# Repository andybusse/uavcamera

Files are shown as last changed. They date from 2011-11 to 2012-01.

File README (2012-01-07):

Unmanned Aircraft Camera Module

(Full specification including deliverables for this project is contained in documents/specification/Agreed_Spec_Gantt_GDP18.pdf)

Repository Structure:
- ArduinoCore: An Eclipse project that creates an Arduino library, allowing us to combine Arduino code with AVR C Source code.
- documents: Project Management foo, foo that requires submission (reports, presentations + whatnot), minutes of meetings, etc.
- eclipse:
    - CamPayloadCpp: source code for the payload controller firmware (not all ours)
        - mod: existing code from our customer
	- sanguino: code from the sanguino project (http://sanguino.cc)
	- SoftwareSerial - the SoftwareSerial library for Arduino/Sanguino (http://www.arduino.cc/en/Reference/SoftwareSerial)
	- SD: the SD library for Arduino/Sanguino (http://www.arduino.cc/en/Reference)
    - progressiveJPEG2: our current work on progressive jpeg encoding/decoding
- ExtractorExecutable: final version of custom JPEG extractor code (from progressiveJPEG2)
- FinalReport: our final report. RC2 is the version as handed in. Includes a CD with this repository at revision b0a90776af
- gettingJPEGdataInC: reads data from the camera and inserts this into a table.
- jpegCheaderExtractor(_nonavr): our current work on progressive jpeg encoding/decoding
- jpeghuffman: generates a huffman tree from a given JPEG image.
- Matlab: Matlab code to test custom image compression methods.
- NCamGS: Code for our ground station image viewer (C#, Visual Studio 2010 project)
- programAVR: Slightly modified from sample_peripheral, code intended to be run on a DIP version of the ATmega168.
- progressiveJPEG2: our current work on progressive encoding/decoding
- sample_peripheral: Schematics and Code for a simple AVR-based peripheral for the autopilot module. Supplied by the customer.
- schematics: A full set of schematics, PCB layout and gerber files generated using gschem and PCB from the gEDA toolsuite. Run "$ gschem $NAME.sch 
- uCode: Arduino "sketch" code, written for an Arduino Uno, designed to communicate with our chosen camera, implementing the commands defined in the datasheet (linked to within documents/)
    - SPI_debugger: code for the SPI debugger, based on an example project in the Arduino IDE (http://www.arduino.cc)

This project also contains some code which we have not authored:
    - ArduinoCore (from http://www.arduino.cc)
    - eclipse/ArduinoCore (from http://www.arduino.cc)
    - eclipse/ArduinoBlinkTest_Template (from http://www.arduino.cc)
    - eclipse/CamPayloadArduino/SD (from http://www.arduino.cc/en/Reference)
    - eclipse/CamPayloadArduino/SoftwareSerial (from http://www.arduino.cc/en/Reference/SoftwareSerial)
    - sample_peripheral - existing code, provided by our customer (see below)
    - programAVR - essentially contains the same as sample_peripheral, just in a AVR Studio 5 project.

A Group Design Project (ELEC6050) - School of Electronics and Computer Science, University of Southampton.

GDP Group 18 Members:
Andrew Busse <Andrew.Busse@zepler.net>
John Charlesworth <jgac1g08@ecs.soton.ac.uk>
Michael Hodgson <mh23g08@ecs.soton.ac.uk>
Paramithi Svastisinha <ps6g08@ecs.soton.ac.uk>
Piyabhum Sornpaisarn <ps26g08@ecs.soton.ac.uk>

Supervisor: Dr. Rob Maunder <rm@ecs.soton.ac.uk>
Customer: Dr. Matt Bennett <m.bennett@skycircuits.com>

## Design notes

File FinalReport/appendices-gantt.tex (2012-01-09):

% This is part of the FinalReport document.
% Copyright (C) 2011 Piyabhum Sornpaisarn, Andrew Busse, Michael Hodgson, John Charlesworth, Paramithi Svastisinha
% See the file COPYING in FinalReport/ for copying conditions.

\label{appendix:gantt}
This section shows the Gantt Charts produced for this project. The first one, 
displayed over the first three pages, shows our initial Gantt chart, as 
produced for handin with the specification (10th October 2011).

The second, shown over pages 4 to 6, shows a revised version of our Gantt 
Chart, produced on 8th November 2011.

The third, shown over pages 7 to 9 shows the final version of our Gantt chart as of
15th December 2011.

These Gantt Charts have been produced using the Planner tool from GNOME office.
\footnote{\url{http://live.gnome.org/Planner}}

\includepdf[scale=1.0,pages={1-3},offset=25mm -25mm]{gantt/gantt1.pdf}
\includepdf[scale=1.0,pages={1-3},offset=25mm -25mm]{gantt/gantt2.pdf}
\includepdf[scale=1.0,pages={1-3},offset=25mm -25mm]{gantt/ganttfinal.pdf}

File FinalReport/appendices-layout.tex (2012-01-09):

% This is part of the FinalReport document.
% Copyright (C) 2011 Piyabhum Sornpaisarn, Andrew Busse, Michael Hodgson, John Charlesworth, Paramithi Svastisinha
% See the file COPYING in FinalReport/ for copying conditions.

\label{appendix-layout}

The layout of the final PCB module. As seen in figure \ref{fig:PayloadImplementation} 

This was made using PCB \footnote{\url{http://geda.seul.org/wiki/geda:gaf}} from the gEDA toolsuite.

Gerber files, and full source files, are available in our central GitHub 
\cite{github} repository, under schematics/payload\_644.pcb and schematics/gerbers

Running
\begin{verbatim} 
$ gsch2pcb projectrc
\end{verbatim}
from within schematics/ should update any changes you make to payload\_644.sch.

\begin{figure}[H]
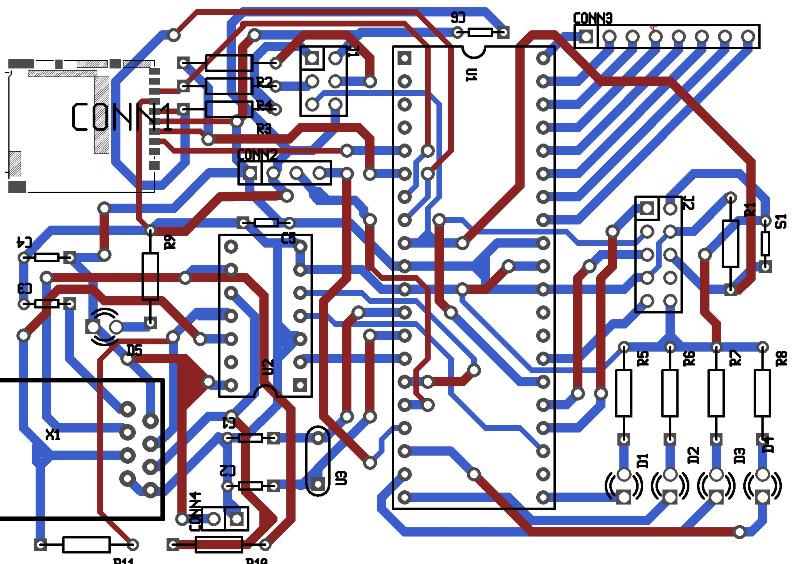
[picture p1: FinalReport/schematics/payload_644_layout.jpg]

\caption{Layout of our delivered PCB module. Dark Red: component layer. Light Blue: solder layer}
\end{figure}

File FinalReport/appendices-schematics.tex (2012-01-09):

% This is part of the FinalReport document.
% Copyright (C) 2011 Piyabhum Sornpaisarn, Andrew Busse, Michael Hodgson, John Charlesworth, Paramithi Svastisinha
% See the file COPYING in FinalReport/ for copying conditions.

\label{appendix_schematics}

All schematics in this Appendix were generated using gschem from the gEDA 
toolsuite. \footnote{\url{http://geda.seul.org/wiki/geda:gaf}}

These are all available in our GitHub repository \cite{github}, under the 
schematics/ folder. PDF and PS files are also available in the 
schematics/images folder.

Note that you need to run 
\begin{verbatim} 
$ gschem SCHEMATIC_NAME
\end{verbatim}
from within this folder to use the non-standard symbols available in that 
folder.

\section{Dummy Payload}
\begin{figure}[H]

\caption{Schematic of the circuit used to test communication from a "dummy" 
payload to the autopilot module. Largely based on a schematic provided by 
our customer, and runs a slightly modified version of source code provided 
again, by our customer.}
\end{figure}

\section{Final Payload Module}
\label{Payload_Schematic}
\begin{figure}[H]

\caption{Final Schematic of the implemented payload module. See \ref{fig:PayloadImplementation} for a 
detailed explanation of which components are for what purpose}
\end{figure}

\section{Payload: Arduino Uno with additional ATmega168}
\begin{figure}[H]

\caption{Schematic for a considered payload module: an 
Arduino Uno with a daughter board containing an ATmega168 for Autopilot to 
Payload module communication.}
\end{figure}

\section{Payload: Arduino Uno with Multiplexed UART line}
\begin{figure}[H]

\caption{Schematic for a considered payload module: an 
Arduino Uno with its UART line multiplexed between camera and autopilot 
communication}
\end{figure}

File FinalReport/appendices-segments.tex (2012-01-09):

% This is part of the FinalReport document.
% Copyright (C) 2011 Piyabhum Sornpaisarn, Andrew Busse, Michael Hodgson, John Charlesworth, Paramithi Svastisinha
% See the file COPYING in FinalReport/ for copying conditions.

\section{SOF0: Start Of Frame (0xc0):}

\begin{table}[!hbtp]
	\label{sof-content}
	\caption{SOF0 Marker Content}
	\centering
	\begin{tabular}{ | p{2cm} | p{1.5cm} | p{4cm} | }
	\hline
	\textbf{Field} & \textbf{Size} & \textbf{Comments} \\ \hline
	Length & 2 bytes & Equal to 8 + the number of components used in the colour scheme * 3\\ \hline
	Data precision & 1 byte & Value shown in bits/sample. Usually 8 signifying bytes.\\ \hline
	Image height  & 2 bytes & ----\\ \hline
	Image width  & 2 bytes & ----\\ \hline
	Number of components & 1 byte & indicates the number of components used  in the colour scheme\\ \hline
	Component information & 3 bytes / component & See component information table below.\\ \hline
	\end{tabular}
\end{table}

\begin{table}[!hbtp]
	\label{sof-comp-content}
	\caption{SOF Component Information}
	\centering
	\begin{tabular}{ | p{2cm} | p{4cm} | }
	\hline
	\textbf{Byte Number} &  \textbf{Information} \\ \hline
	1 & Component ID (1 = Y, 2 = Cb, 3 = Cr, 4 = I, 5 = Q)\\ \hline
	2 & Sampling factors (bits 0\ldots3 : vertical, bits 4\ldots7 horizontal)\\ \hline
	3 & Quantization table number\\ \hline
	\end{tabular}
\end{table}

\newpage

\section{DHT: Define Huffman Table(s) (0xc4):}

\begin{table}[!hbtp]
	\label{dht-content}
	\caption{DHT Marker Content}
	\centering
	\begin{tabular}{ | p{2cm} | p{1.5cm} | p{4cm} | }
	\hline
	\textbf{Field} & \textbf{Size} & \textbf{Comments} \\ \hline
	Length & 2 bytes & ----\\ \hline
	HT Information & 1 byte & See HT Information table below\\ \hline
	Number of Symbols  & 16 bytes & Number of symbols with codes of length 1\ldots16.
	The sum of these values (\emph{n})must be $\le$ 256\\ \hline
	Symbols  & \emph{n} bytes & Symbols of the HT in order of increasing code length\\ \hline
	\end{tabular}
\end{table}

\begin{table}[!hbtp]
	\label{dht-info-content}
	\caption{HT Information Byte Content}
	\centering
	\begin{tabular}{ | p{2cm} | p{4cm} | }
	\hline
	\textbf{Bit} &  \textbf{Information} \\ \hline
	0\ldots3 & ID number of HT\\ \hline
	4 & type of HT, 0 = DC table, 1 = AC table\\ \hline
	5\ldots7 & Unused\\ \hline
	\end{tabular}
\end{table}

\section{DQT: Define Quantization Table(s) (0xdb):}

\begin{table}[!hbtp]
	\label{dqt-content}
	\caption{DQT Marker Content}
	\centering
	\begin{tabular}{ | p{2cm} | p{1.5cm} | p{4cm} | }
	\hline
	\textbf{Field} & \textbf{Size} & \textbf{Comments} \\ \hline
	Length & 2 bytes & ----\\ \hline
	QT Information & 1 byte & See QT Information table below\\ \hline
	Bytes  & \emph{n} bytes & QT values. \emph{n} = 64 * (QT precision + 1) \\ \hline
	\end{tabular}
\end{table}

\begin{table}[!hbtp]
	\label{dqt-info-content}
	\caption{QT Information Byte Content}
	\centering
	\begin{tabular}{ | p{2cm} | p{4cm} | }
	\hline
	\textbf{Bit} &  \textbf{Information} \\ \hline
	0\ldots3 & ID number of QT\\ \hline
	4\ldots7 & precision of QT (0 = 8 bit, else 16 bit)\\ \hline
	\end{tabular}
\end{table}

\newpage

\section{SOS: Start Of Scan (0xda):}

\begin{table}[!hbtp]
	\label{sos-content}
	\caption{SOS Marker Content}
	\centering
	\begin{tabular}{ | p{2cm} | p{1.5cm} | p{4cm} | }
	\hline
	\textbf{Field} & \textbf{Size} & \textbf{Comments} \\ \hline
	Length & 2 bytes & Equal to 6 + 2 * (number of components in scan)\\ \hline
	Number of components in scan & 1 byte & Within range 1 to 4\\ \hline
	Component information & 2 bytes / component & See component information table below.\\ \hline
	Ignorable Bytes & 3 bytes & Separates header information from entropy-encoded image data\\ \hline
	\end{tabular}
\end{table}

\begin{table}[!hbtp]
	\label{sof-comp-content}
	\caption{SOS Component Information Content}
	\centering
	\begin{tabular}{ | p{2cm} | p{4cm} | }
	\hline
	\textbf{Byte Number} &  \textbf{Information} \\ \hline
	1 & Component ID (1 = Y, 2 = Cb, 3 = Cr, 4 = I, 5 = Q)\\ \hline
	2 & HT to use (bits 0\ldots3 : AC Table ID, bits 4\ldots7 DC Table ID)\\ \hline
	\end{tabular}
\end{table}

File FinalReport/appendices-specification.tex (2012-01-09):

% This is part of the FinalReport document.
% Copyright (C) 2011 Piyabhum Sornpaisarn, Andrew Busse, Michael Hodgson, John Charlesworth, Paramithi Svastisinha
% See the file COPYING in FinalReport/ for copying conditions.

\label{initial_spec}

This Specification is our specification as it was submitted on to C-BASS 
on Monday 10th October 2011

\includepdf[scale=1.0,pages={1,2},offset=14mm -20mm]{spec/Agreed_Spec_GDP18.pdf}

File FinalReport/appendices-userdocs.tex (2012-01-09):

% This is part of the FinalReport document.
% Copyright (C) 2011 Piyabhum Sornpaisarn, Andrew Busse, Michael Hodgson, John Charlesworth, Paramithi Svastisinha
% See the file COPYING in FinalReport/ for copying conditions.

\label{userDocs}

\includepdf[scale=1.0,pages={1,2,3,4,5,6,7},offset=14mm -20mm]{docs/userGuide.pdf}

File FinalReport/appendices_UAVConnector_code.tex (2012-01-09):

% This is part of the FinalReport document.
% Copyright (C) 2011 Piyabhum Sornpaisarn, Andrew Busse, Michael Hodgson, John Charlesworth, Paramithi Svastisinha
% See the file COPYING in FinalReport/ for copying conditions.

\lstset{numbers=left,
numberstyle=\footnotesize, 
stepnumber=2,numbersep=5pt}
\section{\texttt{UAVConnector} Class}
\begin{lstlisting}[caption=\texttt{UAVConnector} Class, label=appen:UAVConnector]
using System;
using System.Collections.Generic;
using System.Linq;
using System.Text;
using System.Net.Sockets;
using System.Net.Configuration;
using System.IO;

namespace NCamGS
{
    class UAVConnector
    {
        Socket dataPort = new Socket(AddressFamily.InterNetwork, SocketType.Stream, ProtocolType.Tcp);
        Socket consolePort = new Socket(AddressFamily.InterNetwork, SocketType.Stream, ProtocolType.Tcp);

        public void Connect(byte dataStream)
        {
            try
            {
                dataPort.Connect("localhost", 8802);
                //MessageBox.Show("Connection to Port Name" + portName + "Port Number" + portNumber + "is complete!");
                Console.WriteLine("Data port connection to Port Name {0}  Port Number {1} is complete!", "localhost", 8802);

                // send selection byte to select datastream 0
                byte[] dataStreamSelection = { dataStream };
                dataPort.Send(dataStreamSelection);
                Console.WriteLine("Data stream selection completed.");

                consolePort.Connect("localhost", 8800);
                Console.WriteLine("Data port connection to Port Name {0} Port Number {1} is complete!", "localhost", 8800);
            }
            catch
            {
                Console.WriteLine("Error code\n Unable to connect to UAV:\n Please check that:\n1.The UAV is connected \n2.The program gcs has opened \n3. The program has connect to the UAV\n4.The program has send stream dat\n5. The program as to run testbyte on da");
                //MessageBox.Show("Error code\n Unable to connect to UAV:\n Please check that:\n1.The UAV is connected \n2.The program gcs has opened \n3. The program has connect to the UAV\n4.The program has send stream dat\n5. The program as to run testbyte on da");
            }
        }

        public byte[] GetDataBytes()
        {
            //byte[] getByteSendBytes = new byte[numBytes]; // you need to send 0's to get bytes out for some reason (NOPE, it does not)
            //for(int i = 0; i < numBytes; i++) {
            //    getByteSendBytes[i] = 0;
            //}
            //dataPort.Send(getByteSendBytes);
            byte[] sizeByte = { 0 };
            try
            {
                dataPort.Receive(sizeByte, 1, SocketFlags.None);
            }
            catch
            {
                
            }
            int numBytes = sizeByte[0];
            byte[] recBytes = new byte[numBytes];
            try
            {
                dataPort.Receive(recBytes, numBytes, SocketFlags.None);
            }
            catch
            { 
                
            }
            return recBytes;
        }

        public void SendTextToUAV(string textToUAV)
        {
            char[] toUAVChar = new char[512];
            byte[] toUAVByte = new byte[512];
            byte[] fromUAVByte = new byte[1000];
            byte[] oneByteArray = new byte[1];
            textToUAV += "\n";
            toUAVChar = textToUAV.ToCharArray();
            toUAVByte = System.Text.Encoding.ASCII.GetBytes(toUAVChar);
            try
            {
                int sendByte = consolePort.Send(toUAVByte, toUAVChar.Length, SocketFlags.None);
            }
            catch (SocketException ex)
            {
                Console.WriteLine("ERROR: " + ex.Message);
            }
        }
        public void SendCommand(byte[] command)
        {
            // use to send commmand to the uav
            string toUAV;
            //string fromUAV;
            char[] toUAVChar = new char[512];
            byte[] toUAVByte = new byte[512];
            byte[] fromUAVByte = new byte[1000];
            byte[] oneByteArray = new byte[1];

            toUAV = "payload[0].send_bytes";

            for (int commandByteCount = 0; commandByteCount < command.Length; commandByteCount++)
            {
                oneByteArray[0] = command[commandByteCount];
                toUAV += " 0x" + BitConverter.ToString(oneByteArray);
                //toUAV += " 0x" +System.Text.Encoding.ASCII.GetString(oneByteArray); 
            }

            toUAV += "\n";
            toUAVChar = toUAV.ToCharArray();
            toUAVByte = System.Text.Encoding.ASCII.GetBytes(toUAVChar);
            try
            {
                int sendByte = consolePort.Send(toUAVByte, toUAVChar.Length, SocketFlags.None);
            }
            catch (SocketException ex)
            {
                Console.WriteLine("ERROR: " + ex.Message);
            }
            //Port.Receive(fromUAVByte);
            //fromUAV = System.Text.Encoding.ASCII.GetString(fromUAVByte);
        }

        public void Close()
        {
            dataPort.Close();
        }

    }
}
\end{lstlisting}

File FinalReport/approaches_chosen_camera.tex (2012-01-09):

% This is part of the FinalReport document.
% Copyright (C) 2011 Piyabhum Sornpaisarn, Andrew Busse, Michael Hodgson, John Charlesworth, Paramithi Svastisinha
% See the file COPYING in FinalReport/ for copying conditions.

\section{Camera module}
\label{sec:John_chosen_options}

The camera type chosen was a serial camera as described in \ref{sec:Serial_option}. The particular model chosen was uCam (microCam) or the "Camera Module - Serial JPEG TTL" from the "coolcomponents" website.

The feature set of the uCam is as follows:
	\begin{itemize}
		\item It can output images in both RAW and jpeg formats
		\item It can output RAW images at a range of resolutions:
		\begin{itemize}
			\item 80 x 60
			\item 160 x 120
			\item 320 x 240
			\item 640 x 480
			\item 128 x 128
			\item 128 x 96
		\end{itemize}
		\item It can output jpeg images at a range of resolutions:
		\begin{itemize}
			\item 80 x 64
			\item 160 x 128
			\item 320 x 240
			\item 640 x 480
		\end{itemize}
		\item it can output RAW images with a range of colour settings:
		\begin{itemize}
			\item 2bit Gray Scale
			\item 4bit Gray Scale
			\item 8bit Gray Scale
			\item 8bit Colour
			\item 12bit Colour
			\item 16bit Colour
		\end{itemize}
		\item It will auto-detect baud rates from 14400 to 115200
		\item It has selectable baud rates up to 1228800
		\item Small physical size at 32mm x 32mm
		\item Well documented
	\end{itemize}

The camera was chosen because this feature set meets the specification and also allows for additional functionality, such as setting the resolution, if the full feature set is exploited.

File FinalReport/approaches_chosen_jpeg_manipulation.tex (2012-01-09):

% This is part of the FinalReport document.
% Copyright (C) 2011 Piyabhum Sornpaisarn, Andrew Busse, Michael Hodgson, John Charlesworth, Paramithi Svastisinha
% See the file COPYING in FinalReport/ for copying conditions.

\section{Progressive JPEG Manipulation}

\subsection{JPEG Manipulation}

Prior to knowing the exact speed it would take to send an image from the camera to the ground station, 
it was decided that custom JPEG manipulation would optimize the image further and help reach the target time specified. 
Therefore, tasks concerning the custom manipulation of the JPEG image were planned and worked on at the beginning of the project. 
However, when a working module was constructed, the time needed to send the image was already well within the specified time. 
Because this was the primary advantage of the custom JPEG manipulation process, the task's priority was dropped accordingly.

\subsection{JPEG Data Access}

The dynamic form of data accessing was preferred due to the memory contraints imposed on the device.

\subsection{Entropy-Encoded Data Storage}

The entropy-encoded data will be stored as chrominance pixels for the sake of clarity. 
It is also a method which could be coded more easiliy than seperate component storage. 
This allowed the extractor to work with the progressive JPEG encoder sooner to avoid the task from overrunning.

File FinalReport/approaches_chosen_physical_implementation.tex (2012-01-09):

% This is part of the FinalReport document.
% Copyright (C) 2011 Piyabhum Sornpaisarn, Andrew Busse, Michael Hodgson, John Charlesworth, Paramithi Svastisinha
% See the file COPYING in FinalReport/ for copying conditions.

\section{Physical Implementation}

The physical implementation of the payload has taken many forms, reflecting 
the each of the design-prototype-test cycles that our group experienced.

\begin{itemize}
\item Initially, the system was built in two separate parts: The first was 
the modified version of the ATmega168P-based sample schematic provided by 
our customer, which handled communication to the payload port of the 
autopilot. The second was an Arduino Uno R2 with its Serial (UART) line 
connected to the camera and an SPI connection to an SD card. This system 
simply took an image from the camera and wrote it to the SD card. The SD card 
to Arduino connection was via some protoboard and an SD card reader breakout 
board on loan from Zepler Stores.
\item The next design iteration used an "Il Matto" board and daughter board, 
designed for 2011's D4 lab (a two-week Design and Build exercise for second 
year Electronic Engineers). The board itself is rather simple - an ATmega644P 
with all of its ports connected to expansion headers, an SPI line connection 
to an SD card reader, and power taken from a mini-USB connection, stepped 
down to 3V3 by a linear regulator. A daughter board (which slots into the 
expansion headers) has the transceiver to communicate with the autopilot

This implementation of the payload contains all the elements of the final 
schematic, so technically could be test-flown.
\item Whereas the above approach would technically fulfil the specification, 
implementing it would be expensive: the Il Matto boards were one-off boards 
designed specifically for a lab, so a customer would certainly need to 
manufacture and build their own, including the daughter board. Having this as 
a single PCB solution would be a lot neater, smaller, lighter and cheaper.

Therefore, a final PCB was designed (this is elaborated upon in 
\ref{sec:PCB-implementation}), specific to our application, with all the 
features we need. Only through-hole components are used where possible, 
making the task of soldering components to the PCB as easy as possible.
\end{itemize}

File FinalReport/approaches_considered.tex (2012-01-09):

% This is part of the FinalReport document.
% Copyright (C) 2011 Piyabhum Sornpaisarn, Andrew Busse, Michael Hodgson, John Charlesworth, Paramithi Svastisinha
% See the file COPYING in FinalReport/ for copying conditions.

%% ----------------------------------------------------------------
\chapter{Design Decisions}
%% ----------------------------------------------------------------
Throughout the design and implementation of the project there were many points
at which decisions were made about the design of the system. This chapter attempts
to give an insight into some of the design decisions taken throughout the project with
a discussion of the alternative choices that were open to us at the time and the reasons
why a particular choice was made.

This chapter also details thel milestones of the project. These milestones can be seen in section \ref{sec:amended_milestones}.

\input{approaches_considered_camera}

\input{approaches_considered_local_storage}

\input{approaches_considered_payload}

\input{approaches_considered_jpeg_manipulation}

\input{approaches_considered_GUI}

\section{Physical Implementation (ab)}

Our specification states that the final module delivered to the customer 
should be on PCB, if time permits. Using existing breakout board type devices 
(such as the Arduino) and a daughter board would make the project far cheaper for 
one-off applications (one-off PCBs can be rather expensive) while still fitting 
this specification point, 
but would increase construction time to reproduce it, and increase the weight 
and volume of the module, two critical components of the project.

However, producing a bespoke PCB has the advantage of being smaller 
and lighter, and assembly could be handled by an external company.

Producing a stripboard solution would be implemented only if time and budgetary constraints are against us: 
whilst being the cheapest option, it would be larger than a PCB solution and not as robust.
	
\subsection{Power Source}

We also need to consider how such a module will be powered, and plan for both the following considerations:

\subsubsection{Approach: Battery Powered}

Providing a header on our final payload to attach an external power source 
should the Autopilot not be able to provide enough power would seem a 
sensible option. As this battery is likely to be Lithium-Ion or 
Lithium-Polymer, implementing a charging circuit may be considered, but would 
be dangerous to test. (Lithium Polymer batteries are prone to damage if incorrectly charged)

\subsubsection{Approach: Autopilot Powered}

It should be possible to source enough power from the Autopilot, which can 
comfortably provide up to 200mA at 3.3V. Designing our module to be as low-powered 
as possible would be beneficial (this extends the time the autopilot will be 
able to fly)

\input{milestones_amended}

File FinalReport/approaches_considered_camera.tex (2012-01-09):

% This is part of the FinalReport document.
% Copyright (C) 2011 Piyabhum Sornpaisarn, Andrew Busse, Michael Hodgson, John Charlesworth, Paramithi Svastisinha
% See the file COPYING in FinalReport/ for copying conditions.

\section{Camera Module (jc)}
\label{sec:John_options}

A range of different camera modules were researched and considered for use in the project.

\subsection{Approach: Compact Digital Camera}
\label{sec:Compact_option}
A huge range of compact digital cameras are available for purchase and this was considered as a possible approach.

Advantages:
      \begin{itemize}
         \item High resolution of typically 5+ Megapixels.
		 \item Fully encapsulated.
		 \item High quality images possible thanks to automatic focus and zoom.
     \end{itemize}

Disadvantages:
     \begin{itemize}
        \item Difficult/impossible to communicate with: most modern digital cameras have a USB socket for downloading images off the camera but it is much rarer to be able to send the camera commands (e.g. take photo) and for those cameras where it is possible the command structure is not usually simple.
        \item Requires USB host device in order to properly communicate as only USB host devices provide power via USB and can have USB peripherals connected to them.
	\item Relatively large and heavy compared to the other approaches considered.
	\item Expensive, prices starting around \pounds 60.
     \end{itemize}

In order to communicate with a camera via USB a USB host is required. The process is usually fairly complex so driver is normally used. This is extremely difficult to implement on a device compact enough for use in this project.

\subsection{Approach: USB Camera}
\label{sec:USB_option}
Many USB webcams are available for purchase and this was considered as a possible approach.

Advantages:
      \begin{itemize}
         \item Low cost of typically around \pounds 15.
         \item High resolution of typically 1 to 3 Megapixels.
		 \item Small size of usually less than 50mm by 50mm.
		 \item Cabling included so can be easily positioned in the UAV.
     \end{itemize}

Disadvantages:
\begin{itemize}
     \item Often poorly documented: no datasheets or datasheets aimed solely at use with a computer.
     \item Difficult to communicate with: These devices are usually designed to be used with a computer so communication is usually done using a proprietary driver (a piece of software that defines how to interact with a peripheral). In order to maintain the proprietary nature of these documentation and/or source code is often not available for them.
    \item Requires USB host device in order to properly communicate as only USB host devices provide power via USB and can have USB peripherals connected to them.
	\item High resolution means longer total transfer times, including time to transfer from the camera and time spent on any compression/ manipulation.
\end{itemize}

In order to communicate with a USB camera a USB host is required, and as the process is usually fairly complex a driver is normally used. These drivers are fairly complex pieces of code and they are designed for use on computers, they are also often poorly documented so it would be extremely difficult to implement them on a device compact enough for use in this project.

\subsection{Approach: Analogue Camera}
\label{sec:Analog_option}

Camera modules with analogue composite outputs are available, usually for cctv or surveilence purposes, and were also considered as an approach.

Advantages:
\begin{itemize}
	\item Range of resolutions available.
	\item Small size: usually less than 50mm x 50mm.
	\item This is a mature market so there are plenty of options available.
\end{itemize}

Disadvantages:
     \begin{itemize}
        \item Awkward to communicate with: in order to decode the output of these devices we either need to convert from analogue to digital and then decode the signal (this type of camera usually outputs in composite or component format both of which are complex encodings, particularly when converted to digital) or put the signal through a decoder IC which are better documented but still complex, and the correct chip must be used.
        \item Require case and cabling for placement in UAV.
		\item Can be expensive at up to around \pounds 80.
		\item Often video rather than still cameras.
		\item Often black and white rather than colour.
     \end{itemize}

There are a very wide range of cameras of this type available with different features however there is a significant amount of additional complexity introduced by the requirement to decode the analogue output into something that can be understood by a microcontroller.

\subsection{Approach: Serial Camera Module}
\label{sec:Serial_option}

Some camera modules are available with UART rather than USB serial communications and these to were considered as an approach.

Advantages:
      \begin{itemize}
      	 \item Well documented: these cameras usually come with datasheets and are often designed for use with electronic projects.
		 \item Easy to communicate with as they do not require a USB host or and analogue to digital conversion, additionally most microcontrollers have a built in UART port.
         \item Range of resolutions available.
		 \item Small size: usually less than 50mm x 50mm.
		 
     \end{itemize}

Disadvantages:
     \begin{itemize}
       	\item Require case and cabling for placement in UAV.
	\item Moderately expensive at around \pounds 40.
       	\item The lack of case means that the camera is susceptible to shorts and static.
     \end{itemize}

The ability to communicate via UART combined with the good documentation should allow for control to be established fastest with this camera type.

\section{Approach Chosen: Serial Camera module (jc)}
\label{sec:John_chosen_options}

The camera type chosen was a serial camera as described in \ref{sec:Serial_option}. We chose this camera type because it was the easiest to communicate with as it did not require a USB host or any kind of analogue to digital conversion and decoding. The serial camera type also has most of the advantages of the analogue camera type but is easier to communicate with.

The particular model chosen was uCam (microCam) or the "Camera Module - Serial JPEG TTL" from the "coolcomponents" website.

\begin{figure}[H]
        \centering
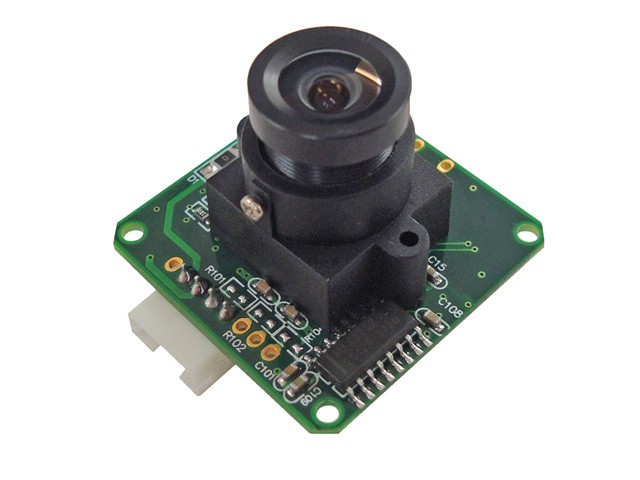
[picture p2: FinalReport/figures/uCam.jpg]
        
        \captionof{figure}{Photo of the 4D systems uCam, sourced from \cite{ucam_datasheet}}
        \label{fig:uCam_photo}
\end{figure}

The feature set of the uCam is as follows:

	\begin{itemize}
		\item It can output images in both RAW and jpeg formats
		\item It can output RAW images at a range of resolutions:
		\begin{itemize}
			\item 80 x 60
			\item 160 x 120
			\item 320 x 240
			\item 640 x 480
			\item 128 x 128
			\item 128 x 96
		\end{itemize}
		\item It can output JPEG images at a range of resolutions:
		\begin{itemize}
			\item 80 x 64
			\item 160 x 128
			\item 320 x 240
			\item 640 x 480
		\end{itemize}
		\item It can output RAW images with a range of colour settings:
		\begin{itemize}
			\item 2bit Gray Scale
			\item 4bit Gray Scale
			\item 8bit Gray Scale
			\item 8bit Colour
			\item 12bit Colour
			\item 16bit Colour
		\end{itemize}
		\item It will auto-detect baud rates from 14400 to 115200
		\item It has selectable baud rates up to 1228800
		\item Small physical size at 32mm x 32mm
		\item Well documented
	\end{itemize}

The camera was chosen because this feature set meets the specification and also allows for additional functionality, such as setting the resolution, if the full feature set is exploited.

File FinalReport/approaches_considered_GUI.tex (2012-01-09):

% This is part of the FinalReport document.
% Copyright (C) 2011 Piyabhum Sornpaisarn, Andrew Busse, Michael Hodgson, John Charlesworth, Paramithi Svastisinha
% See the file COPYING in FinalReport/ for copying conditions.

\section{Ground Station Image Viewer (ps)}

\subsection{Programming Language}

The decision depend on the team member who has been assigned as a task leader.
Because the program will be using to implement a GUI application, therefore it need an object oriented program for implementing this.
The programming languages that will be look into are Python, Javam and C\# programming language.
There are many factors to consider before the final decision is decide.

\subsubsection*{Python Language}
Python Language programming has variety of useful factors for network programming. 
The code on this language has been proved to be short and effective.
The class \texttt{ socket} has all the communication method which can be use. 
The TCP can be use by the program to send a text command on one machine to the another \cite{normanM}. 
There is a makefile function which the user can use to avoid the missing line of data or an extra line from next cycle of data\cite{normanM,guidoR}. 
It has support of GUI interface which the programmer can debug, and use a profiling tools \cite{sannerM}. 

Advantages:
\begin{itemize}
\item has a \texttt{socket()} class which can be use to connect to TCP/IP port
\item support GUI: it can use to create and debugging window application
\item can run with c code
\end{itemize}

Disadvantages:
\begin{itemize}
\item new to the developer
\item might be time consuming to learn if the developer has a same advantages in a familiar software
\end{itemize}

\subsubsection*{Java Language}
Java language is an object oriented program which can be use in any kind of operating system.
It derives some syntax from c/c++ which the developer is familiar to. 
This language has been using widely for applications and gaming and it also support the TCP class.
Java has two classes for TCP/IP, which are \texttt{Socket}, and \texttt{ServerSocket}.
At both ends of the communication can be identified by IP address and port number \cite{kennethC}.

Advantages:
\begin{itemize}
\item it object oriented program 
\item \texttt{Socket} and \texttt{ServerSocket }class support TCP/IP
\item support GUI application
\item has \texttt{graphic} class which can use to display images
\end{itemize}

Disadvantages:
\begin{itemize}
\item it can not inherit other language code to use in the program
\item the developer is not that familiar with the program
\item limit the effectiveness of customs protocols \cite{elliotH}
\end{itemize}

\subsubsection*{C\# Language}
C\# language is an object oriented program which can be use in any operating system.
It has ideally similar Socket class as the Java programming has. 
It also support the window application program.
The program has been use by the developer, therefore it can save time during the implementation of the program.

Advantages:
\begin{itemize}
\item familiar to the developer
\item \texttt{Socket} and \texttt{SerialPort} class support the TCP/IP connection
\item has graphic class which can use to display image
\item can make and debug window application 
\end{itemize}

The program that will be using to implement the program is C\# language. 
This is because the program is familiar with the user so it will save time of studying a new language.
It also support TCP/IP and window application which are main classes needed to implement the program.
Although Java and Python has been use by many papers and book on network programming, but it need to take time to learn a new language so the developer decided to use C\# \cite{normanM,guidoR,kennethC,elliotH}.

\subsection{Approach: Different C\# .NET Classes}
The C\# language on Microsoft Visual Basic Studio is a development environment for creating our Ground Station Image Viewer application. Choosing the right class to connect to the port helps the developer save time to program the application. 
 
\subsubsection{SerialPort Class}
The \texttt{System.IO.Ports} namespace contains classes for controlling serial ports. 
The \texttt{SerialPort} class is the most important one. It has ability to synchronous and event-driven I/O, access to pin and break states, and access to serial driver properties\cite{peak_netFrame}. 
By using this class, the COM port setting has to be memorized which will be simple to load and saves from/to disk.

\begin{lstlisting}[caption=Serial Port class connection\, read and write method, label=serialPortconn]
SerialPort( portName, baudRate, parity bit, dataBits, StopBits ) 
SerialPort.Read(Char(),Int32,Int32);
SerialPort.Write(Char(), Int32, Int32)	;
\end{lstlisting}

Advantage 
\begin{itemize}
\item can change baud rate, handshaking, parity bit, and stop bit
\item can change the internal of a hardware
\item can send and receive data from a defined connection
\item can program hardware
\end{itemize}
Disadvantage
\begin{itemize}
\item need to set up all the component (baud rate, handshaking, parity bit, and stop bit)
\item the set up make the code long and might cause error
\item the setting of the signal out must be the same as the set up in the UAV
\end{itemize}

\subsubsection{Socket Class}
The Socket is more programmer friendly, robust and a high level connection class. 
The program can easily connect to the port by using the method in Listing\ref{socketClasscrs} .
This class sends and array of bytes to the console port and to the data stream port and receive data from the port by code in Listing\ref{socketClasscrs}.

\begin{lstlisting}[caption=Socket class connect receive and send method,label=socketClasscrs]
Connect (String host name,Int32 port number)
Send(byte[] command, Int32 length, SocketFlags)
Receive(byte[] data, Int32 length, SocketFlags)
\end{lstlisting}

Advantage
\begin{itemize}
\item can set up the connection by simply stated the host name and port number
\item can connect to TCP/IP port 
\item it uses the set up of the port, therefore the parity, stop bit, and the baud rate are the same
\item can send and receive data from the port
\item can use delegates which give more flexibility on synchronous control of sockets \cite{robertH}
\end{itemize}
Disadvantage
\begin{itemize}
\item can not program hardware
\item can not set up the baud rate, stop bit or any other properties of the hardware
\end{itemize}

The socket class was the class chosen for the UAV port connector. 
It support TCP connection between the client and the server to do low level communication work\cite{xieX}. 
The changes of class improve efficiency of connection between port and the program. 
The baud rate and extra bits are automatically adjusted to be the same as the port, so the setting is identical between the input and output.

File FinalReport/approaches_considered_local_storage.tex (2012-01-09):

% This is part of the FinalReport document.
% Copyright (C) 2011 Piyabhum Sornpaisarn, Andrew Busse, Michael Hodgson, John Charlesworth, Paramithi Svastisinha
% See the file COPYING in FinalReport/ for copying conditions.

\section{Local Image Storage (ab)}
\label{sec:local_storage}

With a maximum image size of $640\times480$ pixels, an uncompressed JPEG 
image's file size would be approximately 900kB.
This is greater than the internal memory on the ATmega168, ATmega328 and 
ATmega644 (1KiB, 2KiB, and 4KiB respectively) microprocessors that were used 
during development of this project, therefore it cannot be guaranteed that a 
complete single image can be stored locally, without adding some extra memory.
\\
The advantages of being able to store a full image locally are:
\begin{itemize}
\item Would allow all original images taken during flight to be viewed once 
the UAV has been landed.
\item Would make the implementation of automatic repeat requests (resending of 
any corrupted payload -$>$ ground station packets) much easier.
\item Customer mentioned that currently, customers take images with their 
retrofitted cameras, but store the images locally instead of wirelessly 
transmitting them. Keeping the functionality to store all images taken 
on-board and then plug something into the ground station to view these once 
the UAV has been landed would be desirable, but not essential (hence why this 
is not mentioned in the specification).
\end{itemize}

The disadvantages:
\begin{itemize}
\item The material cost of the payload (in both component cost and PCB area) 
would be increased.
\item Addition of an extra component increases the project's complexity.
\end{itemize}

\subsection{Approach: Flash Chip}

One option considered was the implementation of an external flash memory chip 
(for evaluation purposes, the 4Mbit AMIC A25L040-F \cite{flash_datasheet} was purchased)

Advantages:
\begin{itemize}
\item Non-volatile memory. Allows data to be retained even if power to the payload module is cut off.
\item Excellent data integrity: ~100000 Write/Erase cycles, and $>$10 years data retention.
\item Relatively good operating current of ~20mA makes it suitable for battery-powered application.
\end{itemize}

Disadvantages:
\begin{itemize}
\item Chips that contain a significant amount of memory storage (e.g. 1Gbit 
and above), come in packages that are awkward to prototype (BGA, TSOP)
\item Interfacing this type of device with a PC (for debugging) would require a similar amount 
of work to the ground station software.
\item Non-standard interface. The command set for the 4Mbit device is not the 
same as for a 1Gbit device.
\end{itemize}

\subsection{Approach: SD Card}

This is essentially the same as the flash chip above, but with an additional controller chip, and packaged in a standard case.

Advantages:
\begin{itemize}
\item Non-volatile memory. Allows data to be retained even if power to the payload module is cut off.
\item Same data integrity as for the above item.
\item Getting image data from the card would be as trivial as removing the 
card from the payload and inserting it into the ground station laptop. SD card 
readers are cheap, and ubiquitous.
\item Good value for money, when compared to price-per-Mbit of the other two 
options under consideration. (For example, a 2GB microSD card (including 
microSD -$>$ SD adapter) from Amazon costs \pounds4.
\end{itemize}

Disadvantages:
\begin{itemize}
\item Open source libraries can only make use of an SD card's SPI Bus \cite{arduino_sd_library}
interface, not the quicker (but patent-covered) four-bit SD bus.
\item Only standard SD cards are supported, SDHC are partially supported, but not the more recent SDXC cards, which are increasingly popular.
\item File system must be standard (FAT16 or FAT32)
\end{itemize}

\subsection{Approach: SRAM}

SRAM was considered as a possible option as we had all used this before.

Advantages:
\begin{itemize}
\item We have previous experience of interfacing these with AVRs from a 
second-year lab, 
\item This type of memory performs read/write operations much quicker than 
the other two options.
\item Very low operating current of ~10mA makes it suitable for this battery-powered application.
\end{itemize}

Disadvantages:
\begin{itemize}
\item Standard SRAM is volatile, so data is prone to being lost if the payload 
module power is lost, or the payload module is reset. (While non-volatile SRAM 
does exist, it is much more expensive per Mbit (\pounds18/Mbit) than the other 
options under consideration.)
\item Comparatively expensive
\item Communication with the device requires connection to all data, address 
and control pins (or implementation of shift registers with the same desired 
effect), this would require more board space. (The other two devices can 
communicate via an SPI bus, a four wire connection)
\end{itemize}

\subsection{Approach Chosen: SD card}

This approach was chosen as these are very easy to interface with (standard libraries exist), decreasing our development time, 
and they essentially have the same advantages as Flash Chips, plus the ability to easily plug it into a PC.

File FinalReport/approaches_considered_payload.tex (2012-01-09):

% This is part of the FinalReport document.
% Copyright (C) 2011 Piyabhum Sornpaisarn, Andrew Busse, Michael Hodgson, John Charlesworth, Paramithi Svastisinha
% See the file COPYING in FinalReport/ for copying conditions.

\section{Payload Controller Hardware (mh)}
The hardware used to implement the payload controller is an important consideration.

The exact requirements for this module depend on other design decisions made, such as the method used to interface with the camera module. However since the module must communicate with the autopilot over a RS-485 serial connection at 38.4 kBaud this requires the module have access to a UART (Universal asynchronous receiver/transmitter).

%Additional requirements depend on other design decisions:

%\begin{itemize}
%\item \emph{Camera communication:} Using a serial camera would mean the controller requiring access to another UART, while using a USB camera leaves the camera needing access to a USB host interface. Similarly using an analogue camera would mean either the controller be capable of digitising the camera data itself or having a method of interfacing with an external digitiser.
 
%\item \emph{Image buffering:} Most embedded systems do not have enough RAM or Flash to store a reasonable sized image on onboard memory. As described in section \ref{sec:local_storage}, there are a number of approaches worth considering for externally buffering an input image, however these do require the controller to have an interface with which to communicate with the external memory. 

%\item \emph{Progressive JPEG Manipulation:} Section \ref{sec:implementation_progressive_jpeg} details several ways progressive JPEG manipulation could be tackled. Depending on the design choice taken this could influence the requirements of the controller substantially. Examples of such requirements could be: extra processing power, fast access to memory or FFT or DCT libraries being available for the device.
%\end{itemize}

\subsection{Approach: Digital Signal Processor (DSP) Development Board}
An appropriate Digital Signal Processor (DSP) development board would provide fast digital signal processing capabilities to the controller. This would be especially useful for the situations mentioned in section \ref{sec:implementation_progressive_jpeg}.

%Since DSP chips tend to be specialist devices they are usually difficult to set up or program without first experimenting with the design using a development board - a special board designed with experimentation and product development in mind. Ideally a development board would be used for initial development of the system with a integrated PCB being developed later on to allow the DSP to be used on its own.

Advantages:
\begin{itemize}
\item DSPs often have very good analogue to digital conversion built in as standard. If an analogue camera is used a DSP may provide the necessary fast ADC without any extra components.

\item Libraries for tasks such Fast Fourier Transforms or other signal and image processing related applications are often readily available for DSP chips. For some methods of performing progressive JPEG manipulation (see section \ref{sec:implementation_progressive_jpeg}) this could be useful.

\item Large number of miscellaneous signal processing related hardware features built in which could be useful in as-yet unforeseen circumstances.
\end{itemize}

Disadvantages:
\begin{itemize}
\item DSP chips are often complex and may require significant work to produce a system running without a development board.

\item DSP development boards often cannot be used effectively in a final version of a project due to size and power constraints.

\item There is a steep learning curve to using these devices and the group has very little experience with them.
\end{itemize}

DSP boards are a specialist tool, which could be especially useful - if not required - if implementing certain image processing algorithms such as some of those detailed in section  \ref{sec:implementation_progressive_jpeg}. The downside of this is a more complex overall system.

\subsection{Approach: Atmel 8-bit AVR}
\label{sec:desappr:avr}
The Atmel 8-bit AVR family is a well-known set of low cost, single chip microcontrollers. Specific parameters taken from \cite{avr_param}.

Advantages:
\begin{itemize}
\item All members of our group have had experience working with AVR chips.

\item Programming and debugging devices are readily available to us.

\item Creating stand-alone systems easy: no need for large amounts of additional components.

\item Commonly used devices mean large community built around the device family meaning support and additional libraries are more likely to be available.

\item Some initial payload code available to us already implemented on a AVR, see section \ref{sec:team_resources}.

\item Large range of different devices which work with the same programming tools and minimal code changes available.

\item Many through-hole versions of the devices are available, making prototyping significantly easier (and cheaper, due to lack of need for breakout boards) than using surface mount components.
\end{itemize}

Disadvantages:
\begin{itemize}
\item Most 8-bit AVR devices are reasonably low speed (20MHz maximum), meaning they could be unsuitable for heavy calculations such as image processing.

\item 8-bit AVRs do not have floating point processing units, making some image processing tasks much slower to complete on an AVR.

\item Less communication options than some other, more complex, devices. This limits the number of peripheral devices that can be connected to the controller at once.

\item Limited RAM available on the commonly used devices which are available in through-hole format. A common amount of RAM for a larger through-hole AVR is 4 kbytes.

\item The smaller, cheaper, devices have reasonably limited program memory, with 64 kbytes being a typical amount for a larger through-hole device. This could be a problem if implementing large amounts of code.
\end{itemize}
	
AVRs are robust, widely used, general purpose microcontrollers. The large community surrounding them is a particular advantage, as it means many libraries and development boards are available for the devices. Our previous experience with the devices is also a key advantage, although it is important to be aware of the devices limits.

\subsection{Approach: Atmel 8-bit AVR with Arduino Prototyping Platform}
\label{sec:appr_considered_arduino}

The Arduino platform is a low cost, open-source development platform for the Atmel AVR microcontroller family. The latest versions of the development platform consists of an ATMega328 microcontroller along with voltage regulators, inbuilt USB programmer and serial interface and 16MHz crystal. A software library for the device provides a wrapper around many of the complexities of the AVR platform, allowing more rapid development to be possible than with a pure AVR. A simple IDE is used to program the device and a wide range of extra libraries are available which target the platform. The physical platform is designed to be easily extended using expansion boards called `shields'.

The advantages and disadvantages of the Atmel 8-bit AVRs mentioned in section \ref{sec:desappr:avr} also apply.

Advantages:
\begin{itemize}
\item Just an ATMega328 `under the hood' meaning that the additional power of the chip can be leveraged if needed.

\item Many common tasks such as setting the baud rate of the serial link are made very simple by the Arduino libraries, meaning development time can be spent working on more challenging features.

\item Very widely used by hobbyists, meaning a large number of open-source libraries are available for the platform.

\item Platform is easily available meaning others should more easily be able to replicate project. Widely used platform means plenty of support is available for others wishing to re-implement this project.

\item Since only a `shield' expansion board would need to be manufactured this would cut time otherwise spent designing and making board for AVR.
\end{itemize}

Disadvantages:
\begin{itemize}
\item Using the Arduino libraries means a certain amount of unused overhead is likely.

\item The Arduino libraries hide much of the complexity of the device. This can mean advanced features are hidden or not exposed, negating some of the advantages of the library when advanced features are needed.

\item Design would consist of two parts: Arduino board and expansion `shield'. This could reduce durability and increase size.
\end{itemize}

Using an Arduino has the advantage of speeding up development at the beginning of the project. The large number of libraries built for the Arduino is another key advantage, as is the ease of re-implementation.

\subsection{Approach Chosen}
We chose to use an Atmel 8-bit AVR as the platform for our implementation of the payload controller with the use of the Arduino prototyping platform to help speed development. Our main reason for choosing this platform is because we already have experience in using this microcontroller, meaning less time to develop and 
test the system over a DSP based solution. Another key reason was the ease of implementing AVR based systems as 
stand-alone boards.

\section{Communication between Payload Controller and Ground Station (mh)}
\label{sec:appro_cons_pl_gs_comms}
One of the key tasks of the payload controller is to communicate with the Ground Station via the Autopilots 38.4 kBaud serial link. In order to fulfil the specification the payload controller must be capable of receiving messages/commands sent from the Ground Station image viewer software (see section \ref{chap:implementation_ground_station }) through the autopilot link, as well as be capable of sending data to the Ground Station Image Viewer.

The autopilot provides a number of ways to communicate between a payload module and ground station software, see section \ref{sec:autopilot_research}.

\subsection{Approach: Shared Memory for Both Directions}
One possible way of producing two-way communications would involve two sets of shared memory: one for ground station to payload messages and another for payload to ground station messages. Both the payload and the autopilot would need to poll the shared memory to check for new messages.

%Advantages:
%\begin{itemize}
%\item 
%\end{itemize}

Disadvantages:
\begin{itemize}
\item The payload must access shared memory by sending a command to request a copy of its contents to be sent via the payload-autopilot serial link. This extra overhead would slow down communications (such as downloading an image).
\end{itemize}

\subsection{Approach: Send Bytes Command and Shared Memory}
The send bytes command could be used to send messages from the Ground Station to the payload, with shared memory being set by the payload to send messages back from the payload to the Ground Station.

Advantages:
\begin{itemize}
\item No overhead needed to get messages on the payload, they are sent directly from the autopilot to the payload, no polling needed.
\end{itemize}

%Disadvantages:
%\begin{itemize}
%\item Error coding??
%\end{itemize}

\subsection{Approach Chosen: Send Bytes Command and Shared Memory}
Using shared memory for one direction and send bytes for the other seemed like a sensible choice due to the lower overhead needed.

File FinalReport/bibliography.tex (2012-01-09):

% This is part of the FinalReport document.
% Copyright (C) 2011 Piyabhum Sornpaisarn, Andrew Busse, Michael Hodgson, John Charlesworth, Paramithi Svastisinha
% See the file COPYING in FinalReport/ for copying conditions.

\bibliographystyle{ecs}

\begin{thebibliography}{9}

	\bibitem{SkyCircuits} SkyCircuits Ltd. Web. 13th Dec. 2011 \url{http://www.skycircuits.com/}

	\bibitem{SULSA} SULSA \emph{The "Southampton University Laser Sintered Aircraft} Web. 13th Dec. 2011 \url{http://www.soton.ac.uk/~decode/index_files/Page804.htm}

	\bibitem{SC_Press} New Scientist \emph{3D printing: The world's first printed plane} Web. 13th Dec. 2011 \url{http://www.newscientist.com/article/dn20737-3d-printing-the-worlds-first-printed-plane.html}

	\bibitem{SC2} SkyCircuits \emph{SC2 autopilot module} Web. 14th Dec. 2011 \url{http://www.skycircuits.com/autopilot/sc2}

	\bibitem{tortorella_jpeg_enc} Tortorella, Richard. \emph{Image Doctoring: JPEG Encoding and Analysis}. Rep. NARCAP, May 2009. Web. 11 Oct. 2011. \url{http://www.narcap.org/reports/narcap_IR-01_DigHoaxing.pdf}.
	
	\bibitem{exif_std} Japan Electronics and Information Technology Industries Association (JEITA). \emph{Digital Still Camera Image File Format Standard (Exchangeable Image File Format for Digital Still Cameras: Exif)} Version 2.2. Tech. Japan Electronic Industry Development Association (JEIDA), 12 June 1998. Web. 14 Oct. 2011 \url{http://www.exif.org/Exif2-2.PDF}.
	
	\bibitem{netravali_digital_repr} Netravali, Arun N., and Barry G. Haskell. \emph{Digital Pictures: Representation and Compression}. New York: Plenum, 1988. Print. 
	
	\bibitem{jpeg_layout} \emph{JPEG File Layout and Format}. Original URL: \\http://www.funducode.com/freec/Fileformats/format3/format3b.htm (defunct).\\DCube Software Technologies, 5 July 2002. Web. 28 Oct. 2011. \url{http://class.ee.iastate.edu/ee528/Reading%20material/JPEG_File_Format.pdf}
	
	\bibitem{winzip_jpeg_compression} WinZip® International LLC. \emph{JPEG Compression}. Tech. Version 1.0. 11 Sept. 2008. Web. 28 Oct. 2011. \url{http://www.winzip.com/wz_jpg_comp.pdf}.
	
	\bibitem{poynton_chroma_subsampling} Poynton, Charles. \emph{Chroma Subsampling Notation.} Charles Poynton. 24 Jan. 2008. Web. 31 Oct. 2011. \url{http://poynton.com/PDFs/Chroma_subsampling_notation.pdf}.
	
	\bibitem{kerr_chroma_subsampling} Kerr, Douglas A. \emph{Chrominance Subsampling in Digital Images}. Rep. Issue 2. 3 Dec. 2009. Web. 31 Oct. 2011. \url{http://dougkerr.net/pumpkin/articles/Subsampling.pdf}.
	
	\bibitem{hass_impulse_jpeg} Hass, Calvin. \emph{ImpulseAdventure - Digital Photography Articles.} 2008. Web. 22 Nov. 2011. \url{http://www.impulseadventure.com/photo/}.
	
	\bibitem{ucam_datasheet} 4D Systems. \emph{uCam Serial JPEG Camera Module Data Sheet} 8 Jul. 2010. \url{http://www.4dsystems.com.au/downloads/micro-CAM/Docs/uCAM-DS-rev4.pdf}.

	\bibitem{software_serial} Arduino. \emph{SoftwareSerial Library.} Web. 9th Dec. 2011 \url{http://www.arduino.cc/en/Reference/SoftwareSerial}.

	\bibitem{arduino_sd_library} Arduino. \emph{SD Library.} Web. 10th Dec. 2011 \url{http://www.arduino.cc/en/Reference/SD}.
	
	\bibitem{arduino_serial_library} Arduino. \emph{Serial Library.} Web. 1st Dec. 2011 \url{http://www.arduino.cc/en/Reference/Serial}.

	\bibitem{atmega644p} Atmel. \emph{ATMega644P} Web. 10th Dec. 2011 \url{http://www.atmel.com/dyn/products/product_card.asp?part_id=3896}

	\bibitem{sanguino} Sanguino. \emph{What is Sanguino?} Web. 10th Dec. 2011 \url{http://sanguino.cc/}.

	\bibitem{mbed} mbed. \emph{Welcome to mbed!} Web. 10th Dec. 2011 \url{http://mbed.org/}.

	\bibitem{olimexino} Olimex. \emph{Olimexino-stm32 development board Users Manual} Web. Oct. 2011 \url{http://www.olimex.com/dev/DUINO/OLIMEXINO-STM32/OLIMEXINO-STM32.pdf}.

	\bibitem{github} Github. \emph{Our "Official", Central Repository} Web. 11th Dec. 2011 \url{https://github.com/uavcamera/uavcamera}

	\bibitem{go-naked} \emph{Spirit Circuits Go Naked} Web. 11th Dec. 2011 \url{http://www.spiritcircuits.com/services/go-naked}
	
	\bibitem{peak_netFrame} C.D. CĂLEANU, V. TIPONUŢ, I. BOGDANOV, S. IONEL, I. LIE \emph{C\# and .NET Framework for uC communication protocol Proceedings of the 11th WSEAS International Conference on COMPUTERS, Agios Nikolaos, Crete Island, Greece, July 26-28, 2007
implementation} 2008. Web. 22 Nov. 2011.
\url{www.wseas.us/e-library/conferences/2007cscc/papers/561-338.pdf}.

	\bibitem{tsuiK} Kakit Tsui \emph{Ad Hoc Network:Generic USB Device Driver Development} (2003)
\url{http://crisp.ece.cornell.edu/mengproj/alan_report.doc}.

	\bibitem{keithC} Keith Clark,Peter J. Robinson,Richard Hagen.(2001) Multi-threading and message communication in Qu-Prolog.\textit{Theory and Practice of Logic Programming} . 1 (3), p283-301 
	
	\bibitem{davidW} Keith Clark,Peter J. Robinson,Richard Hagen.(2004) \textit{Beginning .NET game programming in C\#.} United States of America: Apress. 

	\bibitem{xieX} Xiaoyun Xie.(2004) \textit{Distributed Objects System in C\#.} Rochester, United States of America. 

	\bibitem{davidB} David B. Makofske, Michael J. Donahoo, Kenneth L. Calvert.(2004) \textit{TCP/IP sockets in C\#  practical guide for programmers}. Amsterdam: Elsevier.

	\bibitem{normanM} Norman Matloff. (2009) \textit{Tutorial on Network Programming with Python}. California

	\bibitem{guidoR} Guido van Rossum. (1994) \textit{Extending and Embedding the Python Interpreter}. The Netherlands

	\bibitem{sannerM} M. F. SANNER. (1999) \textit{PYTHON: A PROGRAMMING LANGUAGE FOR SOFTWARE
INTEGRATION AND DEVELOPMENT}. California

	\bibitem{kennethC} Kenneth L. Calvert, Michael J. Donahoo. (2008) \textit{TCP/IP Sockets in Java
Practical Guide for Programmers}. Kentucky:Elsevier

	\bibitem{elliotH} Elliot R. Harold, Michael J. Donahoo. (1997) \textit{Java Network Programming}. USA:O'Reilly, p35

	\bibitem{ucam_test_software} 4D Systems. Web. 13th Dec. 2011. \url{http://www.4dsystems.com.au/prod.php?id=82}.

	\bibitem{robertH}Robert Harkness and Malcolm Crook and David Povey.(2007) \textit{Programming Review of Visual Basic.NET for the Laboratory Automation Industry}. Journal of the Association for Laboratory Automation vol.12, p.25-32.
	\url{http://www.sciencedirect.com/science/article/pii/S1535553506005302}.

	\bibitem{gpl} GNU \emph{The GNU Public License version 3} Web. 14th Dec. 2011 \url{http://www.gnu.org/licenses/gpl-3.0.html}

	\bibitem{ccbysa} Creative Commons \emph{Attribution-ShareAlike 2.0 UK: England \& Wales (CC BY-SA 2.0)} Web. 14th Dec. 2011. \url{http://creativecommons.org/licenses/by-sa/2.0/uk/}
	
	\bibitem{fdl} GNU \emph{The GNU Free Documentation License version 1.3} Web. 14th Dec. 2011. \url{http://www.gnu.org/copyleft/fdl.html}

	\bibitem{Huffman} D.A. Huffman \textit{A Method for the Construction of Minimum-Redundancy Codes}. Proceedings of the I.R.E. Sept. 1952. p1098-p1102

	\bibitem{avr_param} Atmel.\textit{megaAVR Parameters} 15th Dec. 2011. \url{http://www.atmel.com/dyn/products/param_table.asp?category_id=163&family_id=607&subfamily_id=760}

	\bibitem{flash_datasheet} \emph{A25L040-U - 16Mbit Low Voltage, Serial Flash Memory With 100MHz Uniform 4KB Sectors - AMIC Technology} 8 Jul. 2010. \url{http://pdf1.alldatasheet.com/datasheet-pdf/view/244476/AMICC/A25L040-U.html}.

\end{thebibliography}

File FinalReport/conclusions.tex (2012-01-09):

% This is part of the FinalReport document.
% Copyright (C) 2011 Piyabhum Sornpaisarn, Andrew Busse, Michael Hodgson, John Charlesworth, Paramithi Svastisinha
% See the file COPYING in FinalReport/ for copying conditions.

%% ----------------------------------------------------------------
\chapter{Conclusions (ab)}
%% ----------------------------------------------------------------

This section will discuss to what extent we have fulfilled the requirements 
of this project, mainly in terms of our initial specification, including a 
justification for why certain aspects were not met, and an analysis of 
whether the project, as it currently stands, could be reasonably presented to our customer as a working solution.

\section{Commented Specification}

The initial specification is available as Appendix \ref{initial_spec}. 

This is then analysed and justified in Section \ref{chap:specification}

\subsection{Fully Completed Parts}

\begin{itemize}
\item \ref{sec:spec_b} : The mean time to download an image, with no packet 
loss, is 19 seconds ,reference \ref{sec:sys_testing} . This figure is obtained from testing 
with the serial link only.
\item \ref{sec:spec_c} : The combined weight of the electronic module and 
board camera is 57g. Combined with the camera enclosure and ethernet cable 
(i.e. the entire additional weight to the UAV to add our module), this is 70g. \ref{sec:sys_weight}
\item \ref{sec:spec_d} : We are able to get an image resolution of up to 
$640\times480$ pixels. \ref{sec:sys_testing} .
\item \ref{sec:spec_e} : We provide software that prompts the UAV to capture 
an image, download it and then displays it on screen. \ref{sec:ground_station_image_viewer}
\item \ref{sec:spec_f} \ref{sec:spec_h}  : Our software is able to cancel the download of an 
image mid-transmission. When the "Cancel" button is clicked during image transmission, the 
image is saved in its partial form in the local directory, and in its full form 
on the SD card. If it is cancelled before transmission begins, then the full image is still 
written to the SD card.
\item \ref{sec:spec_i} : Our software allows you to select any resolution that 
is featured on the camera, and download an image at that resolution. This feature has been recently 
implemented and tested. 
\item \ref{sec:spec_m} : We are able to transmit colour images as opposed to 
black and white due to our choice of camera - our camera is only able to 
provide colour images. Therefore it is implemented, but only through our 
choice of camera, not through design.
\end{itemize}

\subsection{Partially Completed Parts}

\begin{itemize}
\item \ref{sec:spec_a} : This task was lowered in priority when we discovered 
that our camera compressed JPEG images a lot more severely than we were 
expecting (image files are approximately 30kB in size, we were expecting 
these files to be 900kB in size). To reflect the time invested in this, we 
have produced some code that partially implements this part of the 
specification, available in section \ref{sec:jpg_prog_test}
\item \ref{sec:spec_j} : A progress indictor does exist (Appendix \ref{userDocs}, p7) , but the 
display only indicates the number of packets received - it does not 
indicate the time remaining to download as this includes the time taken to 
capture an image from the camera and to store it on the SD card.
\end{itemize}

\subsection{Incomplete Parts}
\label{sec:incomplete}

\begin{itemize}
\item \ref{sec:spec_g} : Resending of the same image is not implemented. 
This is, however, a low priority task, which could have been implemented 
if we had more time. In theory, this would be rather trivial to implement.
\item \ref{sec:spec_h} 
\item \ref{sec:spec_l} : Automatic image capture at user-specified time 
intervals was another low priority task which we were unable to implement, 
but which should be rather trivial to implement due to the SkyCircuits 
software's scripting interface, but slightly more difficult than the above
two.
\item \ref{sec:spec_n} : Selecting between colour and black-and-white images 
was included in the specification as we considered that this would reduce 
the image transmission time. However, this was not a feature supported 
by our board camera, implementing it on our AVR would be a non-trivial 
process, and the priority to reduce transmission time was reduced as the 
colour image files themselves were much smaller than expected.
\end{itemize}

\section{Deliverables}

This will discuss to what extent we have delivered everything we specified 
in our specification \ref{initial_spec}

\subsection{Hardware}

\ref{sec:deliv_hw} : We have delivered a suitable board camera, and an 
electronic module on PCB which interfaces the camera to the autopilot's 
payload port. All schematics, layouts, gerber files etc. are provided in 
our central Github repository \cite{github}, and as Appendices \ref{appendix_schematics} and \ref{appendix-layout}

\subsection{Software}

\ref{sec:deliv_sw} : The electronic module delivered to the customer is 
presented with firmware loaded on to it, and the user interface software 
presented as an executable file (requiring only that the .NET framework 
is installed on the PC, however this is the same dependancy as for the 
SkyCircuits software). All firmware for the electronic module, as well as 
source code for our executable Ground Station Software, is presented in 

\subsection{Documentation}

\ref{sec:deliv_doc} : Documentation for our Ground Station Software is 
delivered with this project see appendix \ref{userDocs}. It is assumed that our customers' clients are technically competent, therefore documentation on 
how to order a PCB with our gerber files, how to construct the PCB, and how 
to flash an ATmega644P with our source code was deemed unnecessary.

\subsection{Public Repository}

\ref{sec:deliv_git} : All files related to our project are available in our 
central GitHub repository \cite{github}. Most things in there are open-source: source code is licensed under GPLv3 (GNU Public License version 3), 
\cite{gpl}
images (including PCB layouts and schematic designs) are licensed under 
CC BY-SA 2.0 UK (Creative Commons Attribution ShareAlike) \cite{ccbysa}, 
and all documentation under the FDL (Free Documentation License), \cite{fdl}. This is as-requested, and should encourage sharing this information 
amongst our customers' clients.

\section{General Conclusions}

In conclusion, we have presented the customer with exactly what was requested: 
an electronic module that interfaces a board camera with the provided Autopilot 
module, which exploits the Payload feature of the module and copes well with 
the low-bandwidth Serial link.

Not only this, but we have delivered a fully Open-Sourced project that could 
be replicated by anyone with access to a SkyCircuits Autopilot module, and 
accompanying software.

We have mostly fulfilled all of the objectives we set out in our initial 
Specification \ref{chap:specification}, the reason for us neglecting to completely 
fulfil it being either it becoming obsolete (for the high- and medium- 
priority tasks), or a simple lack of time towards the end of the project.

Our customer was satisfied enough with the Il Matto-based solution to be prepared 
to flight-test that, and present it to his customers. We have enhanced 
both the payload module and the Ground Station Software since. 
It is unfortunate that we have not been able to do this 
test before the report deadline, but it is planned to perform this test in 
early January, before the final presentations. All indications point to this 
test flight being successful, should weather conditions be favourable.

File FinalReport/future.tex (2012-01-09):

% This is part of the FinalReport document.
% Copyright (C) 2011 Piyabhum Sornpaisarn, Andrew Busse, Michael Hodgson, John Charlesworth, Paramithi Svastisinha
% See the file COPYING in FinalReport/ for copying conditions.

%% ----------------------------------------------------------------
\section{Future work (jc and ab)}
%% ----------------------------------------------------------------

This section of the evaluation looks at potential additions to this project, 
which we would have done if time permitted. This starts with parts of the 
specification that we were not able to implement, and continues with some 
more advanced additions that we have considered.

\subsection{Ground Station Software (ab)}

The Ground Station Software which we have submitted remains rather buggy. 
There is a memory leakage issue which causes both our and SkyCircuits' 
software to crash after viewing a certain number of images, we have not had the time to resolve. This is not altogether critical, as the software 
is functional, and once re-started will re-connect to the autopilot. 
As the autopilot is autonomous, can take control of an aircraft from takeoff 
to landing, and is subservient to a manual controller, this is not a critical 
issue, but one that 

It is also not feature-complete (see \ref{sec:incomplete}), something which 
could be resolved with some fairly trivial modifications to our code.

\input{future_progressive_jpeg.tex}

\subsection{Video Streaming (ab)}

A rather interesting advancement of this project would be to try and implement 
real-time video streaming from the UAV. This would almost certainly have to use 
a dedicated wireless link. The 38.4 kBaud available in the autopilot modules 
is too restrictive for this sort of application, but the autopilot would still 
be able to control such an application (i.e. able to start/stop transmission, 
toggle power to the module, etc.) but things like 
minimising delay between video capture and video 
display, finding a suitably fast and robust wireless link (which implements 
automatic repeat requests) would make this task a very difficult one. It may 
be preferable to try and hack an existing wireless video module to one's own purposes (if such modules exist and are 
well documented)

\subsection{Using Multiple Cameras (ab)}

Another interesting application would be to mount multiple cameras (of the same 
model purchased for this project) on the UAV, and either take pictures from all 
the cameras at the same time, from some of the cameras at the same time, etc. 
The main issue here will be multiplexing the serial connection to all of the 
cameras, something considered for this project but ultimately not chosen.

\subsection{Using Multiple Types of Camera (ab)}

It would be useful to provide a range of camera modules to the customer, and 
an electronic module that would be able to communicate with all of them. This 
would include all the types of camera we considered (USB, serial and analogue), 
with varying resolutions. This would be rather difficult to implement, as the 
standards used across two types of the same camera interface can be rather 
different, so a driver would need to be written for each type of camera used. 
Also, the budget for such a project would be quite high.

\subsection{SD card filesystem (jc)}

It would be a nice additional bit of functionality if the sd card on the UAV could be accessed as if it were another file system on the computer running the ground station software. This would allow any of the photos stored on the UAV to be viewed easily and would also mean that the UAV could be used as an unusual form of data transfer, carrying files from one place to another.

This would also be useful if the payload was extended to contain other sensors that outputted files of a different type to the jpeg image from the camera.

\subsection{HDR Photography (jc)}

Image processing could be implemented in the image viewer software to enable high dynamic range (HDR) imaging. This could be useful for finding objects within a certain colour/intensity range by expanding the dynamic range over that region.

\subsection{3D photography (jc)}

If multiple cameras are implemented then these could be separated and the images from both combined to form 3 dimensional images, the vertical resolution of the 3d image would be proportional to the separation of the cameras.

An alternate method would be to use a similar method to synthetic aperture radar (SAR) and take one photograph, fly on a bit further and then take another. The speed and/or gps data from the UAV could then be used to work out the distance between the two photographs which could then be fed into the image processing algorithm in order to again generate a 3d image (presuming sufficient overlap within the images).

%\subsection{Camera SD bus}

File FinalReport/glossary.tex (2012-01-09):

% This is part of the FinalReport document.
% Copyright (C) 2011 Piyabhum Sornpaisarn, Andrew Busse, Michael Hodgson, John Charlesworth, Paramithi Svastisinha
% See the file COPYING in FinalReport/ for copying conditions.

\chapter{Glossary}

\section*{Terms} 
\begin{description}
	\item[YCbCr] Colour space used to represent JPEG images. Composed of three values:
		\begin{description}
			\item[Y] luma component.
			\item[Cb] blue-difference chroma component.
			\item[Cr] red-difference chroma component.
		\end{description}
	\item[4:x:y]Chroma subsampling notation.
		\begin{description}
			\item[4] Luma horizontal (and vertical) sampling reference.
			\item[x] Cb and Cr horizontal sampling factor.
			\item[y] Cb and Cr horizontal sampling factor. If 0, indicates 2:1 vertical subsampling for both Cb and Cr.
		\end{description}
\end{description}

\section*{Abbreviations} 
\begin{description}
	\item[IC] Integrated Circuit
	\item[RF] Radio Frequency
	\item[TCP/IP] Transmission Control Protocol/Internet Protocol
	\item[PCB] Printed Circuit Board
	\item[RGB] Red,Green and Blue
	\item[AC] Alternating Current 
	\item[DC] Direct Current 
	\item[JPEG] Joint Photographic Experts Group, creators of the jpeg compression method. Used interchangeably with the jpeg image type.
	\item[EXIF] EXchangeable Image File format for digital still cameras.
	\item[MCU] Minimum Coded Unit
	\item[DPCM] Differential Pulse Code Modulation
	\item[RLE] Run-Length Encoding
	\item[DFT] Discrete Fourier Transform
	\item[FFT] Fast Fourier Transform
	\item[DCT] Discrete Cosine Transform
	\item[WHT] Walsh–Hadamard Transform
	\item[KLT] Karhunen-Lo\`eve Transform
	\item[SOI] Start Of Image
	\item[SOF] Start Of Frame
	\item[DHT] Define Huffman Table(s)
	\item[HT] Huffman Table
	\item[DQT] Define Quantization Table(s)
	\item[QT] Quantization Table
	\item[SOS] Start Of Scan
	\item[EOI] End Of Image
	\item[UART] Universal Asynchronous Serial Receiver/Transmitter
	\item[LOS] Line Of Sight
	\item[USART] Universal Synchronous/Asynchronous Serial Receiver/Transmitter		
	\item[SD(SC) card] Secure Digital (Standard Capacity) card (Capacity $<$= 2GiB
	\item[SDHC] Secure Digital High Capacity (2GiB $<$= Capacity $<$= 32GiB)
	\item[SDXC] Secure Digital eXtended Capacity (32GiB $<$= Capacity $<$= 2TiB)
	\item[UAV] Unmanned Aerial Vehicle
	\item[GPLv3] GNU Public License version 3
	\item[CC BY-SA] Creative Commons Attribution ShareAlike License
	\item[FDL] GNU Free Documentation License
	\item[BGA] Ball Grid Array
	\item[TSOP] Thin Small-Outline Package
	\item[IDE] Integrated Development Environment
	\item[SPI] Serial Peripheral Interface Bus
	\item[JTAG] Joint Test Action Group
\end{description}

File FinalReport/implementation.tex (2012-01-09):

% This is part of the FinalReport document.
% Copyright (C) 2011 Piyabhum Sornpaisarn, Andrew Busse, Michael Hodgson, John Charlesworth, Paramithi Svastisinha
% See the file COPYING in FinalReport/ for copying conditions.

%% ----------------------------------------------------------------
\chapter{Implementation - Payload}
%% ----------------------------------------------------------------
\label{chap:implementation}

\section{Overview (mh)}

The payload controller module is an important part of the system, responsible
for interfacing with the camera module and communicating with the ground 
station image viewer software via the autopilot. Since this single module 
encapsulates a significant amount of the complexity of the project it was 
deemed sensible to split it up into sub-modules, which could be worked on in
parallel by different members of the team. 

With this in mind the payload controller module was split into four main 
submodules:

\begin{itemize}
	\item Camera Module Communication
	\item Communication with Ground Station via Autopilot
	\item SD Card Image Buffering
	\item Progressive JPEG Manipulation
\end{itemize}

%||||||| INCLUDE REFERENCES TO EACH ||||||||||

%||||||| INCLUDE SUBMODULE DIAGRAM OF THE PAYLOAD MODULE |||||||

\input{implementation_camera}

\input{implementation_SD}

\input{implementation_payload_controller}

\input{implementation_progressive_jpeg}

\section{Integration of Payload Sub-Modules (mh)}
\label{sec:int_pl}
%|||||||| REMINDER: DISCUSSION OF ARDUINO MULTIPLEXED SERIAL

\subsection{Integration of Camera Module with SD Card}
Both the camera module and SD card module were initially prototyped and 
partially tested separately,
%|||||| REFS ||||||||
but were integrated at
a fairly early stage. This integration was the easiest way of testing the 
camera module, since the images from the camera could be written to the SD
card, allowing for easy inspection.

\subsection{Integration of Camera Module and SD Card with Payload-Ground Station Communication}
Integrating the camera module with the payload to ground station communications
was a major milestone for the project, since completing it would mean we would
have a basic working system. It was also one of the most challenging parts of
the project. This step was performed iteratively over time, with the most basic
features being implemented, integrated and tested before more advanced features
were attempted

Integration of the Payload-Ground Station communications with the Camera module
was completed on the ATMega644P hardware, please see section \ref{sec:atmega644p_impl}
for more info about this aspect and an idea of the challenges and problems
faced.

\subsection{Integration of Progressive JPEG Manipulation}
Unfortunately due to time constraints we were not able to integrate the
progressive JPEG manipulation code into the payload module, please see section \ref{sec:implementation_progressive_jpeg} for more information.

\subsection{Implementation on Arduino}
\label{sec:implementation_arduino}
Initially we planned to implement the system on the Arduino prototyping 
platform with an expansion `shield' board providing any extra hardware needed -
the reasons for this are discussed in section \ref{sec:appr_considered_arduino}.
The camera module connection code had also already been developed and tested on
the Arduino. 

This plan relied on the implementation of a multiplexed serial solution, where
the single serial port of the Arduino would be used to connect to two different
devices (the camera and the autopilot) at different baud rates and message
formats. It was planned that this would be achieved by the use of tristate
buffers to form a bus with the two devices TX and RX lines. The payload software
could then take care of altering the message format and speed when needed.

Unfortunately, due to time constraints alongside setbacks such as those
discussed in sections \ref{sec:probls_pl} and \ref{sec:cam_prob}
 it was decided that implementing the system on the 
Arduino platform may not the best way to proceed. The main reason for this 
decision was the number of unknowns in the planned multiplexed implementation
- since it was not really how the hardware is designed to be used, it was not
certain it would provide satisfactory results in the limited time that we had.

\subsection{Implementation on ATMega644P}
\label{sec:atmega644p_impl}
Several options were considered alongside the multiplexing option discussed above. One alternative workaround discussed was to use a separate AVR as an interface to the autopilot and connect it to the Arduino using bit-banged SPI or the inbuilt two-wire interface (TWI, sometimes known as I2C). This approach was 
attractive as it meant we could use the existing Arduino code for the camera 
and SD card and use the existing ATMega168 code for the autopilot communication.
However, this solution would add another complex component to the system along
with another communications link, increasing complexity significantly.

Another option considered was using an AVR device with multiple UARTs so one 
could be used for the camera and another for the autopilot link. However, 
the code we had written for interacting with the SD card buffer relied upon 
some Arduino specific libraries. Finding new libraries and rewriting this code 
would be time consuming and inefficient, especially since we had already 
invested time in creating a working SD card solution.

Further investigation into the Arduino SD card library code (for more info
regarding the library see reference \cite{arduino_sd_library}) suggested that
it was coded to work with the ATMega644P chip as well as the ATMega168 and
ATMega328P. Both the ATMega168 and ATMega328P feature only one UART, but the 
ATMega644P features two, making it attractive for use in this project (see
\cite{atmega644p} for more info about the ATMega644P).

Since the ATMega644P provides two UARTs and the SD card library we were using
supported this chip it was decided that using the 644P would be a sensible 
way forward. 

It is important to note that frequent progress reviews meant that the problem of how to implement this integration and the need for 2 serial lines was caught early and controlled before it could become more damaging.

As mentioned above in section \ref{sec:payload_existing_code} the code provided
to us for communication with the autopilot was written for an ATMega168 chip. 
Porting this code and the existing Arduino camera code to the 644P was not a 
trivial task, although it was simplified by the use of the Sanguino library -
a port of the Arduino core libraries to the 644P (see \cite{sanguino}). Some 
changes were made the the Sanguino libraries for use in our project, for 
example the Sanguino handling code for one of the UARTs was disabled to allow
it to be configured manually for autopilot communications. Some small pieces
of code that were causing compilation issues were also modified.

\section{Debug Interface (mh)}
\label{sec:payload_debug_interface}
While the payload module was being developed debugging was a major concern. 
Having access to an oscilloscope very useful when debugging some particularly 
difficult problems.
However, while building the payload module it was clear more complex details 
about the internal state of the program as it was running would be useful.

While prototyping the camera module on the Arduino platform this problem was 
solved by using the \emph{SoftwareSerial} library (for information regarding 
the library see \cite{software_serial}) to send textual debug information via
a serial to USB cable to PC. This proved very useful when prototyping camera
communications.

A slightly different approach was taken when using the ATMega644P. Initial 
testing of the software serial library on this platform suggested that it 
would not work without a significant investment in time fixing it. It was
therefore decided that it would be faster to send debug messages over 
`bit-banged' SPI to a spare Arduino board which then forwarded this data to 
the connected PC over serial. Again, having the use of this debug interface 
proved very useful while implementing the system, and was well worth the 
small amount of extra time taken to develop it.

Figure \ref{fig:debud_conn} shows an example of this debug interface seen on
a serial terminal on a PC.

\begin{figure}[H]
        \centering
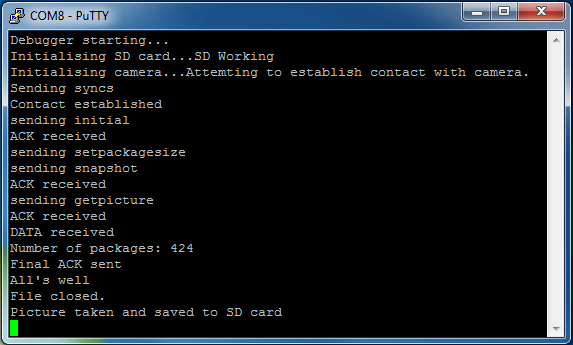
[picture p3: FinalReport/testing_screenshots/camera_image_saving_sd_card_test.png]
        
        \captionof{figure}{Debug text sent from the payload over the debug interface.}
        \label{fig:debud_conn}
\end{figure}

%\section{Development Testing and Debugging (mh)}
%The payload module and submodules were tested throughout development in order 
%to ensure the latest changes and features added were working as expected. 
%This allowed bugs to be caught and fixed as quickly as possible, as well as
%increasing our knowledge of the current state and progress of the system and
%project as a whole.

\input{implementation_physical}

%% ----------------------------------------------------------------
\chapter{Implementation - Ground Station (ps)}
%% ----------------------------------------------------------------

\input{implementation_ground_station}

%% ----------------------------------------------------------------
%\chapter{Implementation - Whole System}
%% ----------------------------------------------------------------

%\section{System Integration}

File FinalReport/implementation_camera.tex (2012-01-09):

% This is part of the FinalReport document.
% Copyright (C) 2011 Piyabhum Sornpaisarn, Andrew Busse, Michael Hodgson, John Charlesworth, Paramithi Svastisinha
% See the file COPYING in FinalReport/ for copying conditions.

\section{Camera Module (jc)}
\label{sec:John_Implementation}

The first step in the implementation of the camera module was to verify the communication with the camera by talking to it via a pc (milestone \ref{sec:ms_img_from_cam}). Once this step was complete the next step was to implement communications between the camera and a microprocessor, with the pc for debugging. With the microcontroller able to communicate with the camera this module was ready for integration with the payload (milestone \ref{sec:ms_img_cam_controller_implementation}).

\begin{figure}[H]
        \centering
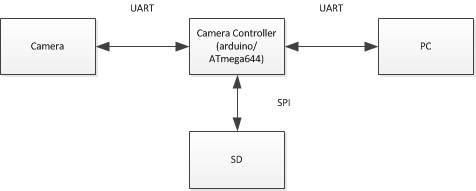
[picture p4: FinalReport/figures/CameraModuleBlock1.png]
        
        \captionof{figure}{Block diagram of the camera module showing where communication takes place}
        \label{fig:camera_block}
\end{figure}

Figure \ref{fig:camera_block} shows how the camera module is broken down separate to the rest of the system. The camera and the camera controller communicate to set up the camera and get images, the camera controller then stores the image to the SD card and debug messages are sent to the computer during these processes so that the camera is less of a black-box.

During the development of the system 2 cameras (uCam \cite{ucam_datasheet}) died on us. The first very early on in development and the second after the system had been effectively finished apart from a few minor tweaks and implementation of some low priority functionality. These component malfunctions were most likely due to the uCam being sensitive to static so after the first one failed we were careful to only handle the second one on an anti-static mat whilst wearing a wrist-strap, however someone must have gotten careless towards the end of the project.

\subsection{First camera}
\label{sec:cam_prob}
The first attempt at communicating with the original camera was done using the arduino uno microcontroller board. The arduino was chosen as the platform for this first communication because it is simple to program and its programming environment provides various useful libraries, for example for serial communication \cite{arduino_serial_library}. The hardware also provides an easily accessible serial port.

The first implementation of this code managed to occasionally sync (see figure \ref{fig:syncProto}) with the camera (milestone \ref{sec:ms_basic_cam_comm}) but would generate errors when trying to send any further commands. After examining the code and the camera's datasheet it was discovered that the camera was only syncing occasionally because the arduino was using a slower baud rate than the camera could auto-detect, after increasing the baud rate on the arduino the camera would sync every time but the code still generated errors after this point.

It was at this point that the first camera broke. It was no longer syncing (or sending back anything at all, verified by oscilloscope readings), where before it had been doing so reliably and so it was checked with the 4D systems software and shown not to be working \ref{sec:existing_software_test}.

\subsection{Second camera}

Once it was established that the first camera was dead a couple of cheaper surface mount camera modules were purchased as possible replacements however making a successful physical (and therefore also communication) connection to these components proved excessively difficult so a new camera of the same type as the previous one \cite{ucam_datasheet} was ordered. The successfull connection test is seen in section \ref{sec:basic_connection_test}, with debug info observed using a serial monitor.

\subsubsection{Serial cable to computer}

The operation of the new camera module was verified using a usb to serial cable connected to a pc which was running the sample program which was provided by the camera's manufacturer \cite{ucam_test_software}. Using this set up it was shown that the camera was working and that it was possible to get images from it, see section \ref{sec:existing_software_test}.

%[] diagram of pin connections []

\subsection{Arduino implementation}
\label{sec:arduino_imp}

With the operation of the camera verified it was reconnected to the arduino board and the code run again with the same result as before: it would correctly sync (see figure \ref{fig:syncProto} and section \ref{sec:basic_connection_test}) but would generate errors when trying to send any further commands. On inspection of the code it became clear that this was because the same serial line was being used for both communication with the camera and debug messages and that these debug messages were interfering with further communications. Debug messages were therefore moved to a software serial line and sent to the computer via the usb to serial cable and observed using a serial monitor.

The code is broken down so that there are functions for each type of command that the camera can receive, functions that verify the responses from the camera and functions that combine these together in the correct sequence in order to perform a useful task with the camera.

\subsubsection{Camera synchronisation}

The first task in communicating with the camera is to synchronise the serial channel, the uCam datasheet \cite{ucam_datasheet} gives the correct protocol to do this.

\begin{figure}[H]
        \centering
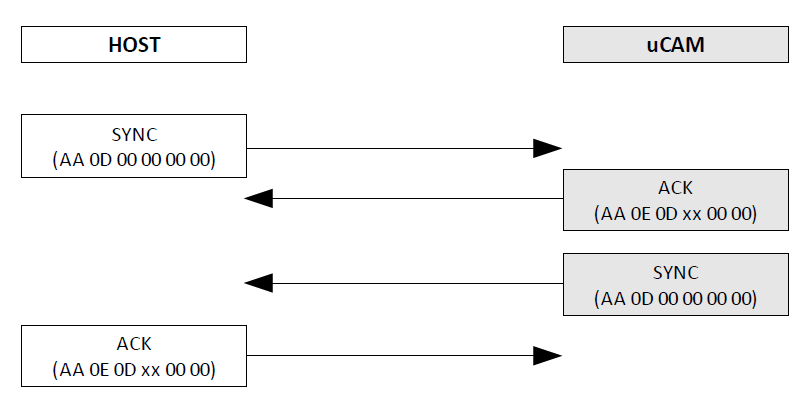
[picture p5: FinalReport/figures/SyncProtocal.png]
        
        \captionof{figure}{Command protocol for synchronisation, sourced from \cite{ucam_datasheet} }
        \label{fig:syncProto}
\end{figure}

It should be noted that in \ref{fig:syncProto} the first sync sent from the host will be repeated until an acknowledgement is received, with everything working correctly this process usually takes 3 or 4 syncs before an ACK is received.

The inclusion of a separate debugging line allows for messages at each stage of this process to verify that it is connecting correctly and to indicate where any errors may have occurred. With all debug messages enabled this function will output "Sending syncs" followed by a "." for each sync command sent and then "ACK received" and "SYNC received", the main code will then output a message to the effect that contact has been successfully established.

\subsubsection{Taking a snapshot}

With the camera successfully synchronised the controller needs to be able to trigger the camera to take a photograph and then retrieve said photograph, again the uCam datasheet \cite{ucam_datasheet} gives an example of how to implement this.

\begin{figure}[H]
        \centering
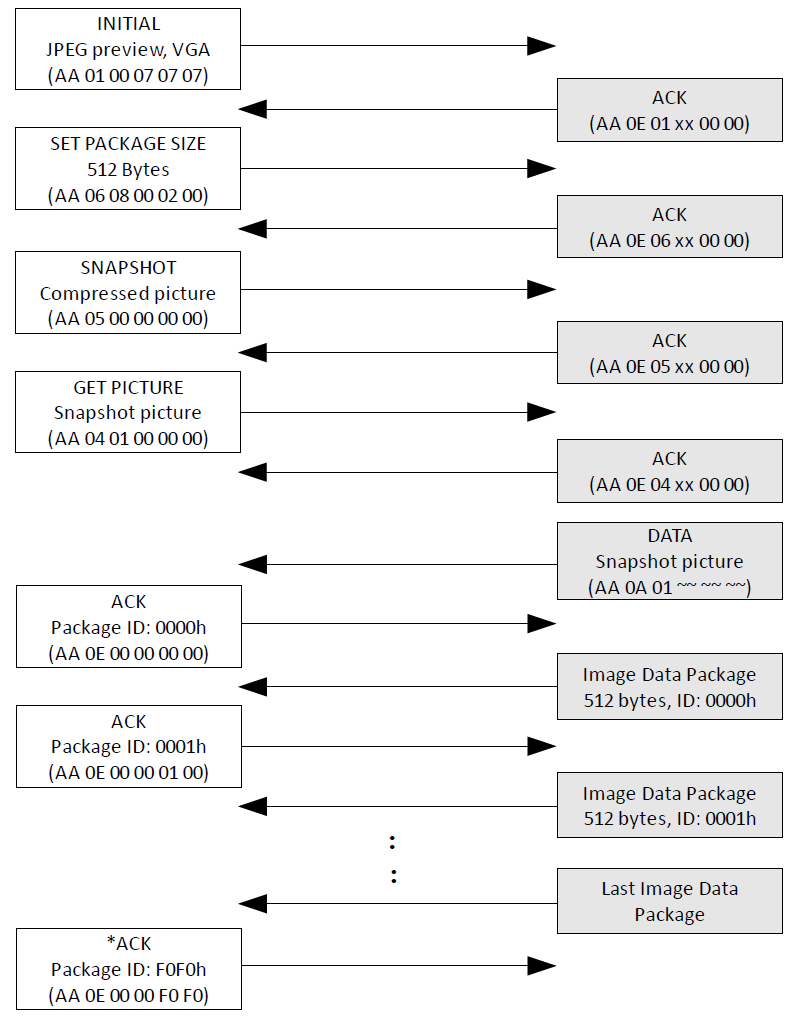
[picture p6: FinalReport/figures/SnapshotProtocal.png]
        
        \captionof{figure}{Command protocol for taking and retrieving a jpeg snapshot at 640x480 resolution, sourced from \cite{ucam_datasheet} }
        \label{fig:snapProto}
\end{figure}

It should be noted in \ref{fig:snapProto} that the values in the commands are for the example and are not necessarily the values used in the code.

The "INITIAL" command has parameters that allow the image type and resolution to be set, in \ref{fig:snapProto} the image type is set to JPEG and the resolution is set to 640x480, these values are kept as the standard in the code.

The "SET PACKAGE SIZE" command is only relevant for jpeg images and set the size of the data packages that are sent when one requests an image. In \ref{fig:snapProto} this value is set to 512 bytes however in the code this is set to 64 bytes as it was originally thought that the system might have to transmit these packages as soon as receiving them so they needed to be a reasonable size to fit in with the timing between transmit packets sent by the autopilot.

The "SNAPSHOT" command tells the camera to take a single picture, its parameter sets whether the image is jpeg compressed or raw, in \ref{fig:snapProto} this is set to be a jpeg image and this is left as the default in the code.

The last command sent by the controller is the "GET PICTURE" command which tells the camera to send image data, it has one parameter which sets which image is sent. In \ref{fig:snapProto} this is set to send the snapshot image and this is also how it is set in the code. As well as sending back an ACK this function will also send back a "DATA" message which tells the controller what type of image is being returned and how large it is.

Once the controller has acknowledged the "DATA" message the camera starts to send data packages, each of which needs to be acknowledged, until the entire image is transferred. Whilst this process is going on the data packages are saved to an SD-card as described in section \ref{sec:SD_imp}.

The use of the debug communication channel again allowed for detailed analysis of this process with the maximum amount of debug messages being one before each command is sent saying what that command is and another message once and ACK is received, there is also then a message with the size of the data in and then messages with the package number and the byte number within that package, the data can also be output to the debug channel, see section \ref{sec:image_capture_test}.

\subsection{Miscellaneous Problems}
\label{sec:misc_cam_probs}

Before the SD-card was implemented the sending of the data directly via the debug channel was attempted and so was its reconstruction into a jpeg image on the computer, this could not be made to work however, see section \ref{sec:image_capture_test}. On looking at the data as it came off the arduino via the software serial debug line it became clear (particularly when looking at the counting values, whose values were already known) that the data was not being transmitted reliably. This could have been because of noise on the line, the fact that the software serial line is communicating via pins on the arduino that aren't optimised for the function or simply failings in the arduino software serial library \cite{software_serial}. For this reason this method of getting an image was abandoned, this also had to be taken into consideration whilst thinking about the integration of this part of the system: the software serial line is not a reliable method of transmitting the data so some other method would have to be used.

Another problem that was noticed after the camera control had been integrated into the payload controller, as described in section \ref{sec:int_pl}, was that every other time the system was powered up the camera would require a reset/power cycle. This was discovered to be because the Rx wire to the camera was left floating, this was fixed by the addition of a 10k$\Omega$ pull-up resistor, see appendix \ref{appendix_schematics} for schematics.

It was also noticed quite early on that the camera required 3.3V logic \cite{ucam_datasheet} levels but the arduino outputs 5V logic levels, the arduino could receive logic at 3.3V easily enough but the 5V output was causing occasional errors. In order to fix this problem the 5V output from the arduino was taken through a potential divider of a 10k$\Omega$ resistor and a 3V zener diode.

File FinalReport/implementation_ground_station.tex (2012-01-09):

% This is part of the FinalReport document.
% Copyright (C) 2011 Piyabhum Sornpaisarn, Andrew Busse, Michael Hodgson, John Charlesworth, Paramithi Svastisinha
% See the file COPYING in FinalReport/ for copying conditions.

\label{chap:implementation_ground_station }

On the ground station the user only has access to the image viewer program.
The programmer makes use of both the data stream port and the console port to send commands to and receive JPEG photos from the UAV.

\section{The development process} 
Because the GUI includes many functions on the application and links to the TCP/IP ports, the GUI part consider as a very big program. 
Therefore, in order to complete the GUI step by step, a plan for the development is required.
The connection to the datastream can be done by using a console application described in section\ref{sec:testing_connection_send_to_stream}.
When the connection is established, the appliction can listen to the data stream port as in section\ref{sec:testing_receive_stream}.
These console applications will be incorporated into a larger program in later section \ref{completeSystem}. 

These are the development stages that the GUI has went through:

\flushleft
\begin{enumerate}

\item	Understanding what the customer wants. 

\item	Determining the hardware and software specifications.
 
\item	Designing the GUI.

\item  Developing a smaller program which simulates the UAV camera's signals in order to make the testing easier and less time consuming. 

\item	Learning the .NET class that can support the connection to TCP/IP, and communicate between the host and device.

\item	Using GUI to link the ground station software to access the UAV.

\item	Distributing the GUI.
\end{enumerate}

\section{Initial Use Case Diagram}
The use case diagram shows what functions the user can use in the program.
It includes all the specification that the customer wants for a complete system.
Figure~\ref{GUI_useCase} shows all possible actions the user can perform on the program, such as saving, opening and deleting any JPEG image from the computer. 
The user can also connect to the UAV if it is not already connected.
He can use the image viewer program to prompt the UAV payload to return an image which will be displayed on the picture box.
\begin{figure}[H]
\begin{center}
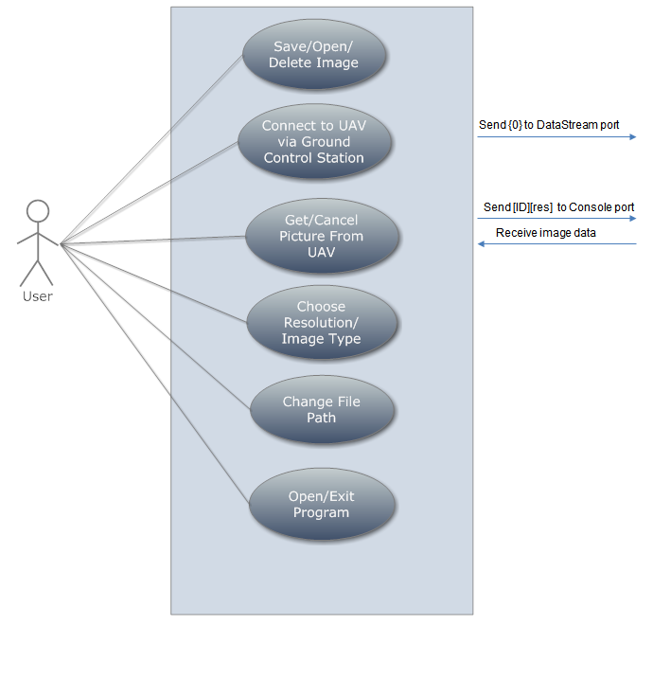
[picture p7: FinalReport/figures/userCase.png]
 
\end{center}
\caption{Use case diagram of the GUI\label{GUI_useCase}}
\end{figure}

\begin{figure}[!hbtp]
\begin{center}
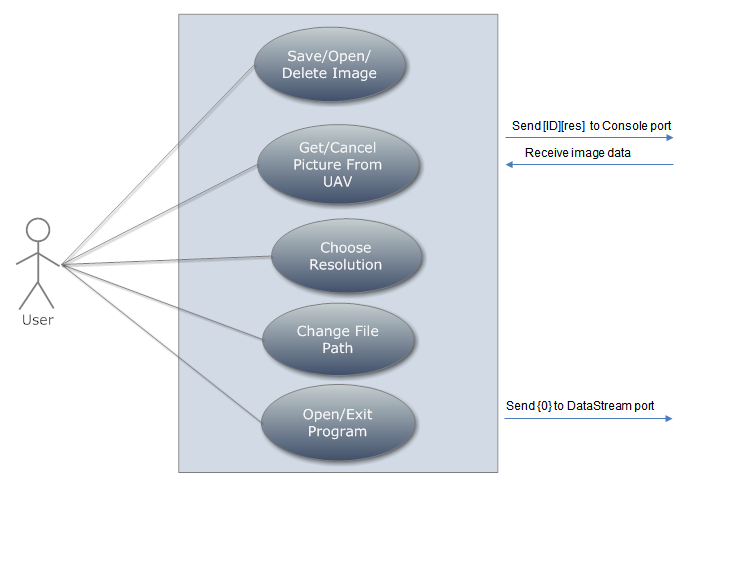
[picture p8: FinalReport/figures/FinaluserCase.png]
 
\end{center}
\caption{Final use case diagram of the GUI\label{GUI_finalUseCase}}
\end{figure}

\section{The Design}

The user of our application is assumed to have limited programming experience, so the program will need to be simple to understand. Figure~\ref{ini_GUI} show the first prototype view of the GUI. 
During the downloading process, the application should stay active so that the cancel button can be used. 
The \texttt{Gallery} button will link to another page which will show a gallery of images taken. 
The \texttt{Left} and \texttt{Right} buttons can navigate the picture box to view an earlier picture or a later picture. 
The \texttt{Cancel} button will cancel the download of the receiving image, so that corrupted pictures can be cancel. 
The user mode of the application can access only the main features, such as taking picture, changing directory, and cancelling the download of a picture.  
It allows the user to choose the resolution and picture type (raw or JPEG) to be transmitted from the UAV to the ground station. However, the user doesn't have access to changing the command sent, changing the receiving data, and any interaction with the UAV because to avoid of any errors.
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

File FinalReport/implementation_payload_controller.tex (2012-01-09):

% This is part of the FinalReport document.
% Copyright (C) 2011 Piyabhum Sornpaisarn, Andrew Busse, Michael Hodgson, John Charlesworth, Paramithi Svastisinha
% See the file COPYING in FinalReport/ for copying conditions.

\section{Communication with Ground Station via Autopilot (mh)}
\label{sec:payload controller}
Considering the overall aim of this project: to produce a system by which 
images can be downloaded over-the-air from a payload module to a ground
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

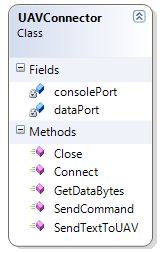
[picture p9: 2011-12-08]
FinalReport/figures/connector_class.jpg

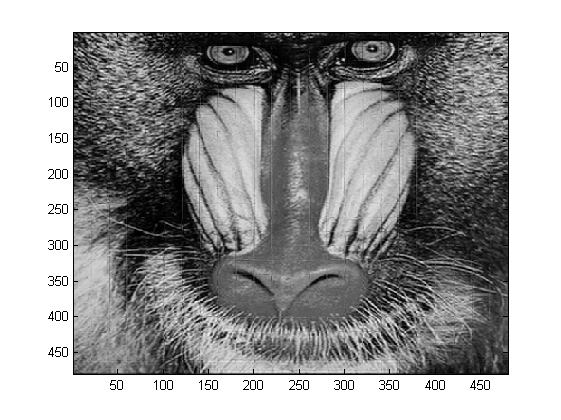
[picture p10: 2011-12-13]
FinalReport/figures/sectioned_fft_mfc.png

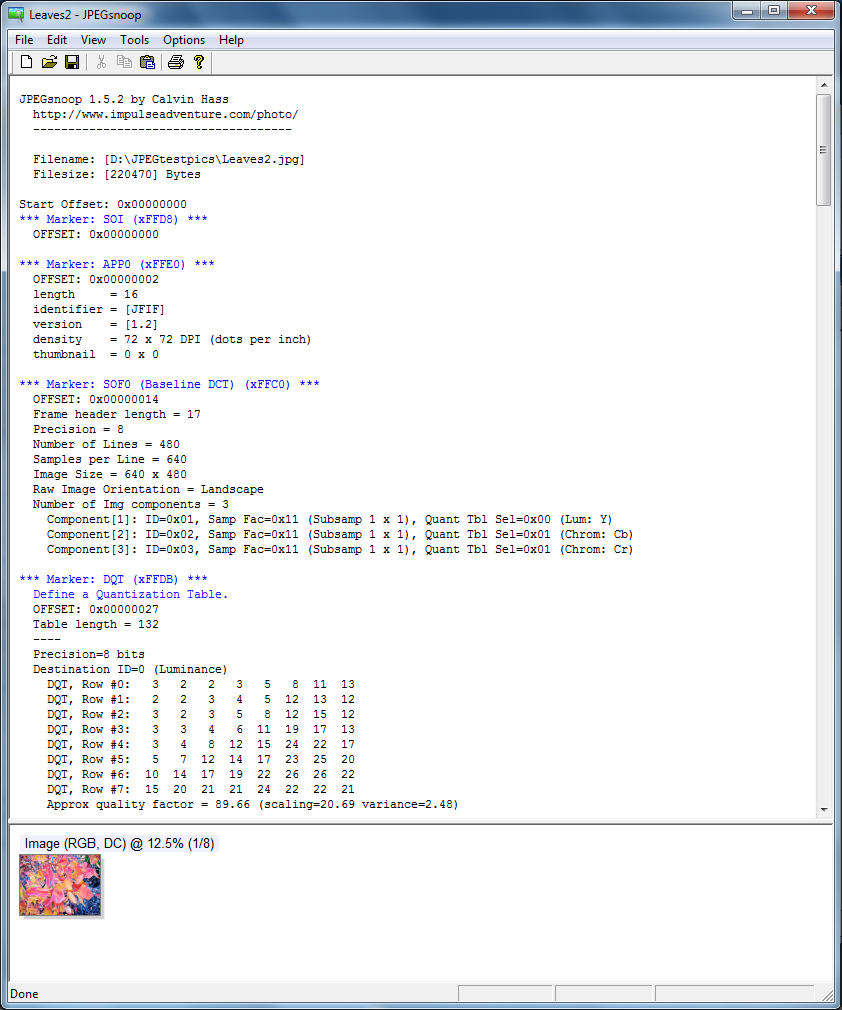
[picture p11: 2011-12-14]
FinalReport/figures/jpegSnoopEx1.png

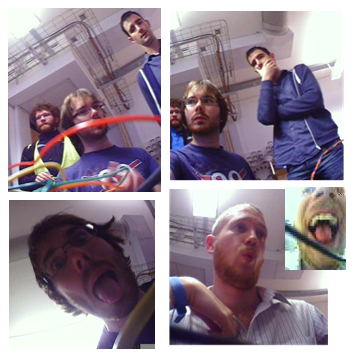
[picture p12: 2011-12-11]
FinalReport/figures/SampleImages1.png

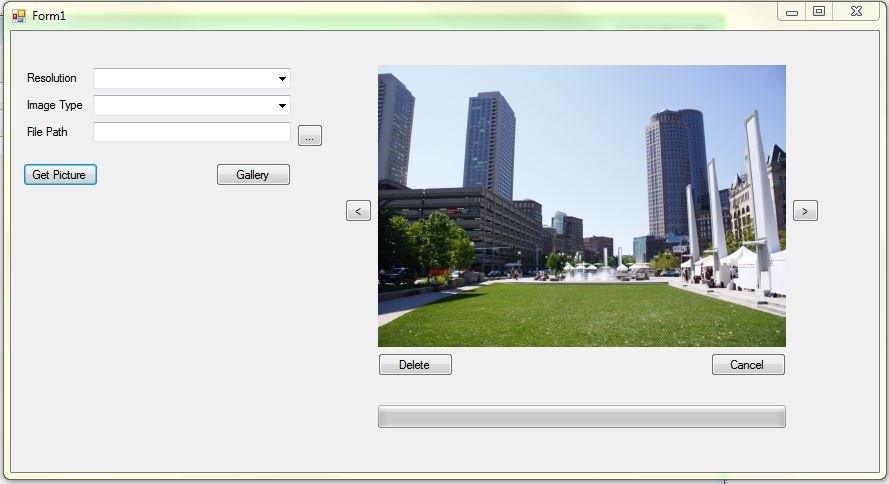
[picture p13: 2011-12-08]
FinalReport/figures/initialGUI.png

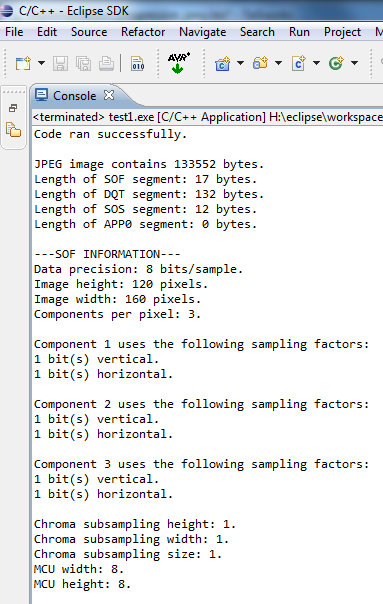
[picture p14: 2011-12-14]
FinalReport/figures/SOFOutput.png

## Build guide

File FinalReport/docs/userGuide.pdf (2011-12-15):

## UAV Image Viewer User Guide

GDP Group 18

December 15, 2011

## 1 Before Starting the UAV Image Viewer Program

In order to connect the payload and camera to the UAV, the user needs to connect an ethernet cable between the Autopilot and Payload modules. The Autopilot powers the payload module, as well as providing a medium for the two modules to communicate. The user should not have to connect the camera manually as it should already be connected.

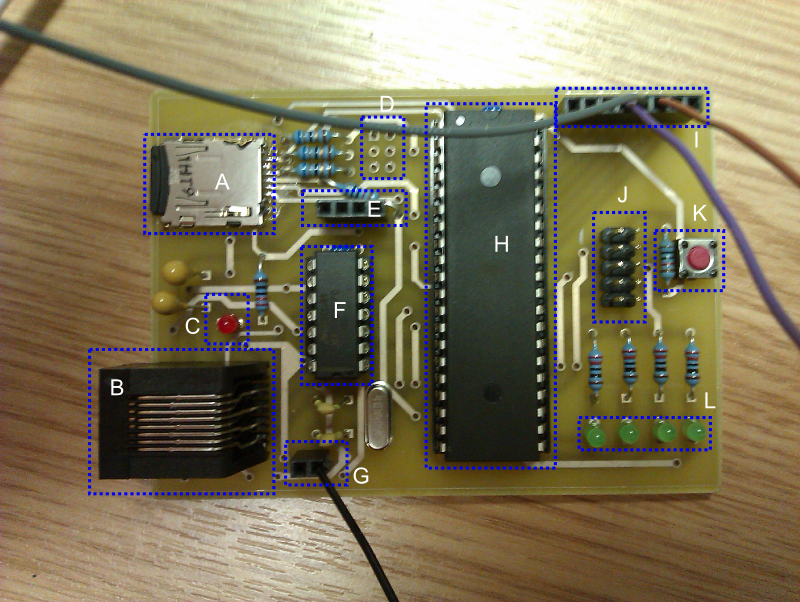
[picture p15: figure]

Figure 1: The Payload Module

Please check the following features on the payload once it has been connected to the Autopilot and the Autopilot is powered:

- The Power LED (C) should be lit.

1

- A microSD card should be present in socket (A). It is preferred if this card is SDSC and not SDHC or SDXC standard. Please make sure this card has enough memory to take the images.
- Images stored locally are up to approximately 30kB in size, and are stored in the filename test$NUMBER.jpg (replace $NUMBER with an integer between 0 and 32768)
- If you are using more payload modules than this, and they are sourcing more than 150mA from the Autopilot, please power this payload module externally. On Header G, connect 3.3V to the left-hand, and GND to the right-hand socket.
- (K) is a reset button.
- In case the camera is disconnected, from L-R on (E), are 3.3V, GND, Camera TX and Camera RX. Please refer to the Camera Schematics.
1

Full schematics, PCB layout and Gerber Files are available in our official GitHub repository 2
, in the schematics/ file. On the ground side, the Autopilot’s receiver module needs to be connected to a USB socket. Figure 2 shows the diagram of how to connect the payload to the UAV and the UAV data receiver to the computer.
For the UAV Image Viewer to work correctly, the receiver must first be connected to the ground station. In order to connect to the receiver, all the hardware has to be connected as described above. The GCS station then connects to the Autopilot receiver by clicking on the Connect button. If the program does not connect to the Autopilot automatically, the user can select it from the combo box. Then check the ”Enable Network Server” box. Figure 3 shows a screen shot of the GCS program. If the autopilot does not appear, the user should check the connection of the UAV and make sure that the driver of the USB has already installed.
To install the USB driver:
Run ”Device Manager” → Right click on the UAV → Click on the update driver→ Find the driver (.inf file) → install it → UAV is ready to use.

## 2 UAV Image Viewer Ground Station

The file tab in the top left corner allows the user to open a file, then display it in the picture box, and save this image to a specified directory. It also gives the option to exit the program. Figure 5 shows the diagram of the file tab.

1
http://www.4dsystems.com.au/downloads/micro-CAM/Docs/uCAM-DS-rev4.pdf
2
https://github.com/uavcamera/uavcamera

2

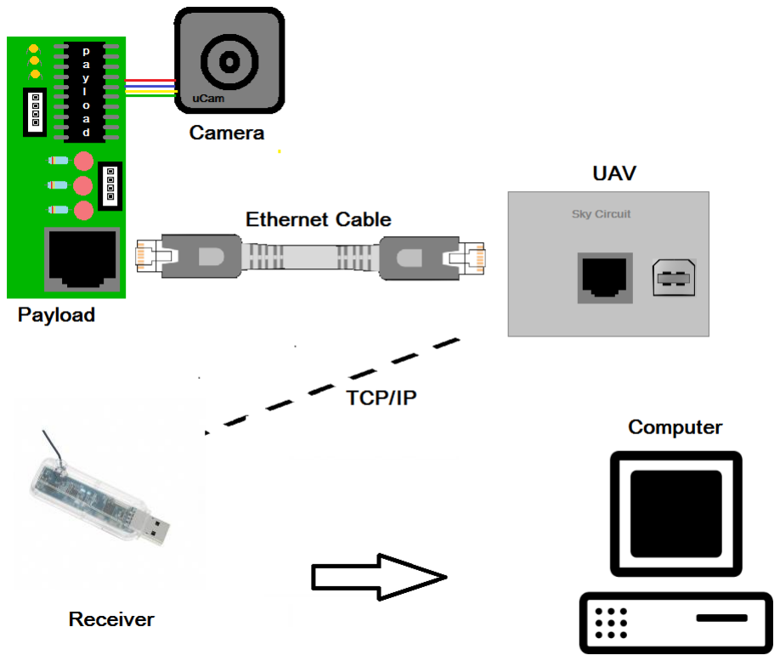
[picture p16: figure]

Figure 2: The Clip Art of the Hardware Connection Diagram

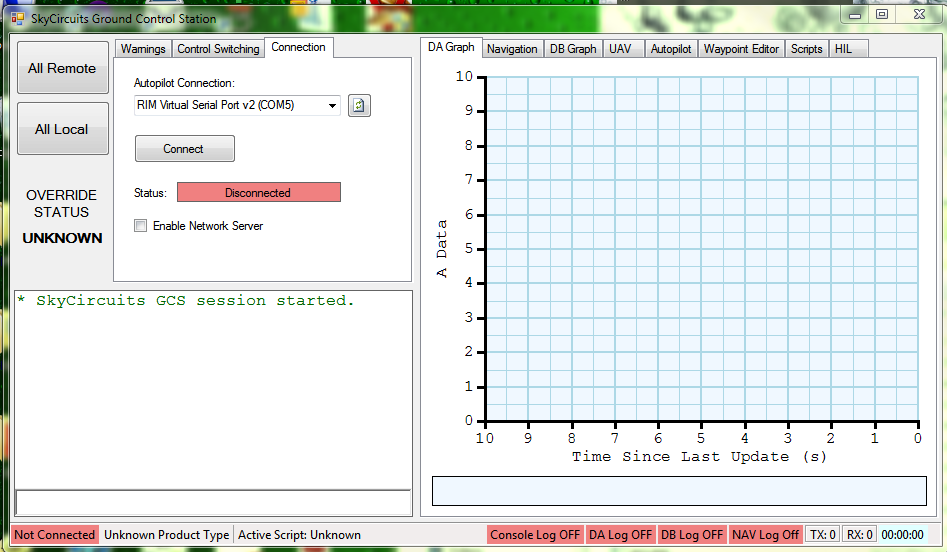
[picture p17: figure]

Figure 3: The Ground Control Station Software

3

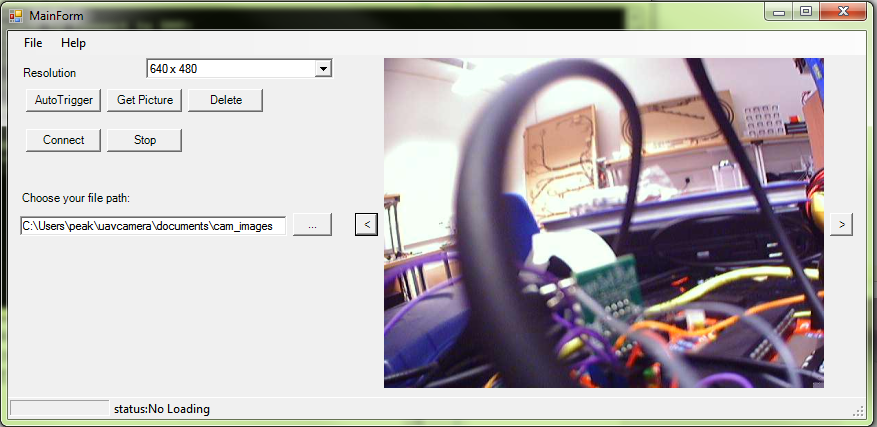
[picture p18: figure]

Figure 4: The UAV Image Viewer Software

Figure 5: Open Tab

4

The user can choose the resolution from the drop-down menu in the top left. There are four options - all of the resolutions that the camera can take. The lower the resolution, the quicker the image downloads.

Figure 6: The Resolution Option

Figure7 shows some buttons present in our application. The AutoTrigger button allows the user to take multiple photos and save them on the on-board microSD card. The Get Picture button will allow the user to take a picture and send it directly to the ground station. The default file name of the picture will be uavPictureAtyyyy-MM-dd hh-mm-ss-tt.jpg. The photo will be saved in the file path specified in the text box as shown in figure 8. The name depends on the system date and time at the time of taking picture. It will take about 10-20 seconds from clicking ”Get Picture” to displaying the image.

Figure 7: The Buttons Options of the Image Picture Viewer

The left and right buttons near the picture allow the user to change the photo displayed to any locally stored jpeg image in the selected file path. The button is shown in figure 9.

5

Figure 8: The file path text box

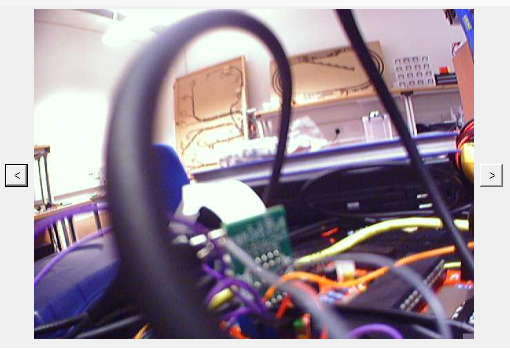
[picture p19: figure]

Figure 9: The Picture Box with left and right buttons

6

The progress bar shows the proportion of the image that has arrived at the ground station. The status label will tell what signal is send and receiving so the user can keep track of what is going on in the payload.

Figure 10: The progress bar and the status text

### 2.1 Take Picture

The use can simply click on the Get Picture button in the program. Figure 7 shows where the button is.

7

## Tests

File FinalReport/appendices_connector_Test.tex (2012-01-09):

% This is part of the FinalReport document.
% Copyright (C) 2011 Piyabhum Sornpaisarn, Andrew Busse, Michael Hodgson, John Charlesworth, Paramithi Svastisinha
% See the file COPYING in FinalReport/ for copying conditions.

\lstset{numbers=left,
numberstyle=\footnotesize, 
stepnumber=2,numbersep=5pt}
\section{Connection class for testing}

\begin{lstlisting}[caption=\texttt{Connector} for testing with console application,label=appen:connectorTest]
    class Connector
    {
        static int requestCounter;
        static ArrayList hostData = new ArrayList();
        static StringCollection hostNames = new StringCollection();
        Socket UAV = new Socket(AddressFamily.InterNetwork,
         SocketType.Stream, ProtocolType.Tcp);

        public byte[] dataFromUAV()
        {
            byte[] uavData = new byte[1];
            byte[] testMessage = {0}; //send zero token to 
            start the datastream port to receive something
            try
            {
                int sendByte = UAV.Send(testMessage, testMessage.Length, 
                SocketFlags.None); //send zero token to the UAV
                Console.WriteLine("Sent {0} bytes.", sendByte); //print on the console
                 so we know what we know
                int size = 8;

                while (true)
                {
                    int byteCount = UAV.Receive(uavData, size, SocketFlags.None);
                     //receive data from the uav of fixed length size
                    for(int countIn=0; countIn<uavData.Length;countIn++)
                    Console.WriteLine("{0}", uavData[countIn]); //
                }
            }
            catch(SocketException uavMessage)
            {
                Console.WriteLine("{0} Error code:{1}.",
                 uavMessage.Message, uavMessage.ErrorCode);
            }
            return uavData;
        }

        public void ConnectToPort()
        {
            const Int32 portNumber = 8802;
            const string portName = "localhost";
            try
            {
                UAV.Connect("localhost", portNumber);
                Console.WriteLine("Connection to Port Name:{0}; Port Number{1} is complete!"
                ,portName,portNumber);
            }
            catch (SocketException uavMessage)
            {
                Console.WriteLine("{0} Error code:{1}.", uavMessage.Message
                , uavMessage.ErrorCode);
            }
        }
    }

\end{lstlisting}

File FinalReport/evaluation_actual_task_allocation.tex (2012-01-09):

% This is part of the FinalReport document.
% Copyright (C) 2011 Piyabhum Sornpaisarn, Andrew Busse, Michael Hodgson, John Charlesworth, Paramithi Svastisinha
% See the file COPYING in FinalReport/ for copying conditions.

\section{Actual Task Allocation (ps)}
In the real work environment, the unexpected situation happens at all time. 
Each members of the group faced different problems.
Some problems were easy to solved but some were very difficult and time consuming. 
The back up plan and unplanned problem solving skills are needed. 
Although many problems happened, but all the team members have been flexible to support each other and problems have been solved quite well. Figure\ref{final task allocation} shows an actual work that each member has done in the project. There are more individual work than the initial allocation because some team members are confident of working alone.

\begin{figure}[H]
        \centering
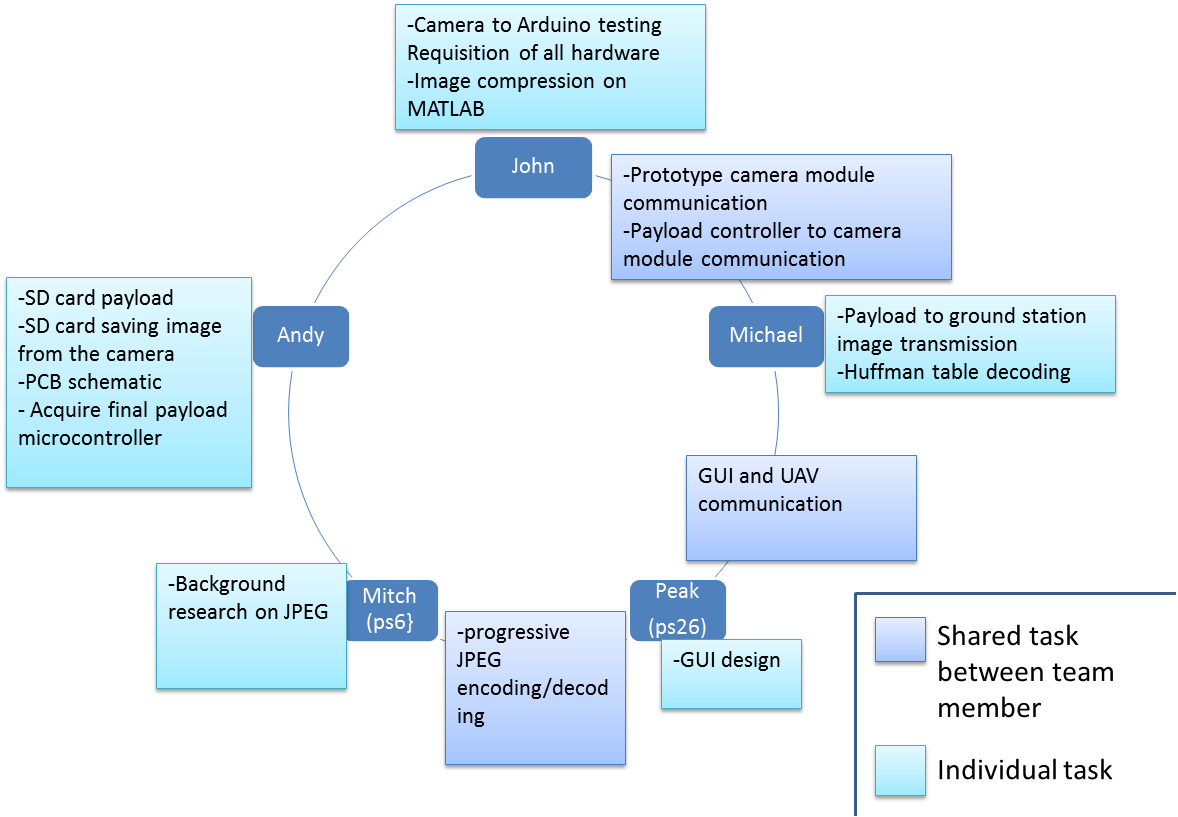
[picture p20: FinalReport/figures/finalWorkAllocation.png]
 
        \captionof{figure}{A diagram show a final work allocation of the team}
        \label{final task allocation}
\end{figure}

Figure \ref{fig:block1} shows a block diagram of the whole system that the developers has slitted in to blocks of tasks. 

The hardwares have uncontrollable acquiring time. 
Some of the group members has problem with the delay of the hardware deliveries. Therefore, the time has to extended longer than the gantt chart. 
So those members were doing other tasks that is hardware independant. 
And at this stage, the background reading is very necessary so the developers has used this waiting time to plan and develop the software, so when the components arrive, all the task can be implemented.

The task that depend on acquiring the camera are the communication between the payload and the camera,prototype camera module, and image encoding. 
The problem that the developers have is the camera delivered is a faulty, the reordered of camera has been taken.
These tasks has been suspended until the camera have arrived.  
Therefore, the new camera has to be purchased and the allocation of work is necessary. 
There are part that is not depended on the hardware such as encoding/decoding images, and ground station software. 
So the members who were assigning to work on the camera has been allocate to do the software part first.

The payload controller has the problem with the hardware part of the UAV. 
It did not respond to the UAV signal at first. 
Therefore, we assign another group member to support this problems. 
The task leader of this has been assigned to do another software module which have to be implemented. 
This problem also need a support from the customer to update the UAV firmware. 
After problem have been noticed, it has been solved successfully. 

The SD card memory task was considered as a small task in the planned work, but in the real implementation it is very important. 
Therefore, we assign on of the member responsible to this task. 
The SD started to implemented after the camera have been arrive and implemented correctly. 

Because there is only one camera purchased, only one member of the team assign to keep the camera. 
There are problems with the cameras including the delay of deliveries, and camera faulty. 
The task leader of this has been assign to research on the progressive image on MATLAB in order to make a prototype presentation of a compression image taken. 
The task has been delayed from the time set to an individual. 
But after the second working camera arrived, the task has been done beautifully and there is enough time to combine with other tasks.

\subsubsection{Schedule - (ms)}
Compared to the planned Gantt chart, some tasks overran significantly (e.g. camera related tasks). The original Gantt chart was updated as we went along, and two of these Gantt charts are shown in appendix \ref{appendix:gantt}. Keeping a Gantt chart was a very useful tool,  because it allowed the group to compare their progress against their plan and therefore identify tasks which are overrunning and take appropriate action. 

Figure \ref{fig:streams} attempts to describe the basic order and integration of tasks with respect to time.

\begin{figure}[H]
        \centering
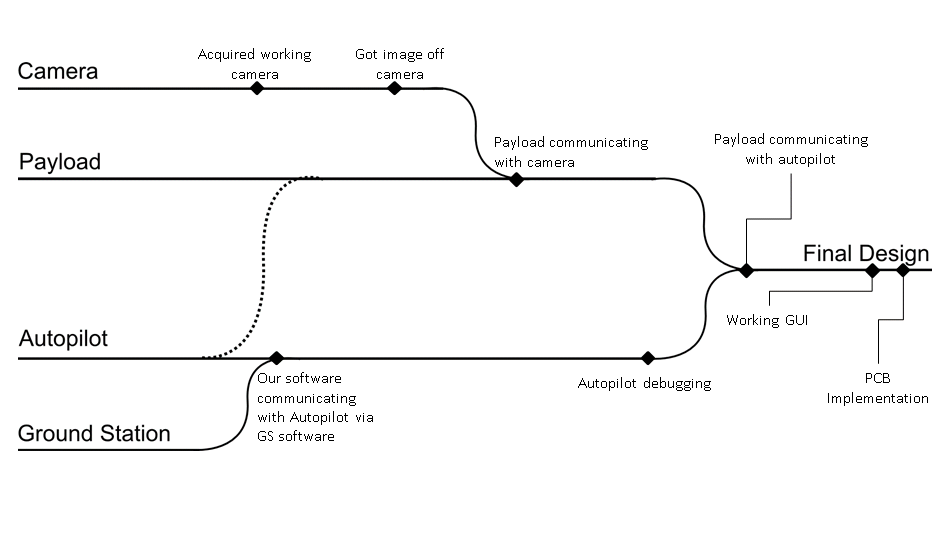
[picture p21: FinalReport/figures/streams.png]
        
        \captionof{figure}{Diagrammatic explanation of the various streams of work and how they combined to produce a successful project.}
        \label{fig:streams}
\end{figure}

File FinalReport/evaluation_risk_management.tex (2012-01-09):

% This is part of the FinalReport document.
% Copyright (C) 2011 Piyabhum Sornpaisarn, Andrew Busse, Michael Hodgson, John Charlesworth, Paramithi Svastisinha
% See the file COPYING in FinalReport/ for copying conditions.

%% ----------------------------------------------------------------
\section{Encountered Risks (ms)}
\label{encountered risks}
%% ----------------------------------------------------------------

\subsection{Encountered Risk: Faulty Components}
Two major components were found to be faulty very early on. 
The first ordered camera module  
arrived in an unresponsive state. 
Due to the price of the device, 
the group preferred attempting to debug the device before 
ordering a new camera module. 
Eventually however, another device needed to be ordered. 
The second camera module lasted for the majority of 
the development process, but also 
become unresponsive during the final weeks of the project,
after the PCB had been received. 
A third camera was ordered immediately for testing purposes.
Choosing a less fragile camera, or taking special precautions
when dealing with the camera would have mitigated this risk better.

The other faulty component was the autopilot module which 
was given to the group by the customer. 
Due to the nature of the autopilot, being a custom component 
from the customer, it was not possible to simply 
order a new autopilot module. 
The group decided to contact the customer for help, and 
worked with the customer to debug the autopilot software 
as discussed in section \ref{sec:probls_pl}.

\subsection{Encountered Risk: Team Members Unavailable}
Some members of the team were too occupied to attend 
all the weekly group meetings and 
the weekly meetings with the supervisor. 
However, this was not a severe problem and individual 
members were always willing to allocate 
meeting times when asked directly. 
The group members were willing to warn the others 
when they would be unavailable for a large period of time. 
This issue did not cause large set-backs in the project.

\subsection{Encountered Risk: Difficulties}
Whenever difficulties were faced, the group member 
facing the difficulty would inform the other 
group members about the problem. 
If the difficulty concerns a high priority task, 
the individual group members would reassign 
tasks to make sure that all the high priority 
tasks were completed as soon as possible. 
Thanks to the skills audit (see section \ref{sec:work_plan}), this made sure that 
any difficulties faced in the high priority 
tasks were taken care of.

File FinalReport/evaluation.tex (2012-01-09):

% This is part of the FinalReport document.
% Copyright (C) 2011 Piyabhum Sornpaisarn, Andrew Busse, Michael Hodgson, John Charlesworth, Paramithi Svastisinha
% See the file COPYING in FinalReport/ for copying conditions.

%% ----------------------------------------------------------------
\chapter{Evaluation}
%% ----------------------------------------------------------------

\input{evaluation_project_management}
\input{evaluation_meeting}
\input{evaluation_communication}
\input{evaluation_risk_management}
\input{evaluation_actual_task_allocation}
\input{evaluation_project_efficiency}

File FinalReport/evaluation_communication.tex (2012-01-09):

% This is part of the FinalReport document.
% Copyright (C) 2011 Piyabhum Sornpaisarn, Andrew Busse, Michael Hodgson, John Charlesworth, Paramithi Svastisinha
% See the file COPYING in FinalReport/ for copying conditions.

\section{Evaluation on Group Communication (ps)}
\label{evaluation on group communication}

\subsection{Source Control}
As describe in section\ref{source control}, there were problems with subversion where some of the files that could not be put into the public folder were accidentally placed there.
This cause some of the group members tries to fixed this problem.
Although the subversion was effective, we have decided to change it to git.
Git is easy to use and all the members can learn it fast and there are no furthur problem.
This save time of combining report because git warn the user when they are submitting something that other member is working on it.
Therefore, all the work flowed well and we have minimized the submission of work problems.

\subsection{E-mail}
The way of communication by email was effective for our group.
Because all the members know how to use it, there is no time wasting on learning a new way of communication.
However, it is likely that some of the group members misread some of the email or did not react to them immediately.
To make this a more powerful way of communication and to ensure that all the members have read the message, the group should have had a rule that on every email, there must be a reply from all of the group member.

\subsection{Supervisor Meeting}
The formal meeting with supervisor that we have described in section\ref{group_comms} has been done successfully. 
In order to make sure these weekly meetings with the project supervisor were fruitful questions were prepared beforehand, to ensure that the project was on track and the most immediate tasks were made very clear.
The customer also came to the meeting once in every two weeks and would evaluate the progress of the project.
This made the project flow smoothly due to having instant feedback from the creator of the UAV module.
The customer's considerate feedback and presence ensured a successful project.
Nonetheless, the group could have made more out of the meetings by showing some of the progress on the report  throughout the project development period.
This would have saved the time needed to finish the report.

\subsection{Telephone (ms)}

Telephone was used rarely. Generally, it was used in 
emergencies, for example, 
when a group member was unable to attend a meeting
and could not inform the others by e-mail. It was also
used when members were unexpectedly absent from 
certain important meetings. Overall, e-mail and 
telephone communication complemented each other well.

\subsection{Internet Relay Chat (ms)}

As the project advanced during the development phase,
more and more tasks required group members working together
in order to be successfully completed. This is due to 
separate modules needing to communicate with each other
and having different people assigned into developing the different modules
in parallel. As this became a more apparent issue, the group adopted
two IRC channels to keep in constant contact with each other.

The first IRC channel was used for development and keeping the 
different module developers in contact with each other as much as possible. 
The second IRC channel was mainly used for the purpose of writing the project
report, due to the large group work involved in creating one cohesive report
from the efforts of different individuals.

Both IRC channels proved invaluable in the later phases of the project, but
due to the individual nature of the early development phases of the project,
were not necessary to be implemented early on. However, it would have been
useful to prepare an IRC at the beginning of the project, if only to have 
another communication tool to help the group members work together.

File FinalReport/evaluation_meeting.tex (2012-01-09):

% This is part of the FinalReport document.
% Copyright (C) 2011 Piyabhum Sornpaisarn, Andrew Busse, Michael Hodgson, John Charlesworth, Paramithi Svastisinha
% See the file COPYING in FinalReport/ for copying conditions.

%% ----------------------------------------------------------------
\section{Group Meeting Evaluation (ms)}
\label{evaluation meeting}
%% ----------------------------------------------------------------

\subsection{Group Meetings}

Having meetings on a weekly basis proved to be very efficient
for the group. Because individual group members met with 
each other on a regular basis throughout the project outside
the weekly meetings, the meetings allowed enough time 
between them to keep them from being redundant.

When certain important deadlines were nearing, the group
would naturally meet up on a more frequent basis and
attempt to tackle important challenges together, even when
no meeting was planned. The meetings allowed the group 
to assess their progress and were vital to avoiding tasks
overrunning.

Minutes of these meetings are available both in our repository \cite{github} 
(documents/minutes), and as an appendix \ref{chap:meeting_minutes}.

\subsection{Minutes Evaluation}

Minutes were taken during each weekly meeting. 
Some minutes were taken during other important meetings 
as well, including meetings with the customer and the 
supervisor. Although, the group member who took 
minutes was not monitored as well as it could have been, 
this did not have any significant effect on the quality 
and/or consistency of the minutes.

The minutes taken were useful for making sure that
all group members were able to check what tasks
they were assigned and catch up on meetings that they
could not assist. The only major setback with the minutes
was the lack of urgency with which they were distributed
to the other group members. Some group members would
update their minutes immediately after the meeting, whereas 
others would not until after the next meeting. Despite
not seriously setting back the project, this undermined the
usefulness of a nonetheless helpful tool.

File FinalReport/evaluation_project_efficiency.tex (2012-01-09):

% This is part of the FinalReport document.
% Copyright (C) 2011 Piyabhum Sornpaisarn, Andrew Busse, Michael Hodgson, John Charlesworth, Paramithi Svastisinha
% See the file COPYING in FinalReport/ for copying conditions.

\section{Evaluation on Project Efficiency (ps)}
The overall design of our project has been done very effectively.
It fully satisfy the high and medium priorities that we has set it.
The project has been done successfully and the outcomes was very pleased by the customer.
However, the project has been changing throughout the time, especially in the hardware part.
The changes on the structure of the payload communication has changed from the planned one.
The SD card has been added to the payload in order to save the picture on board.
It has been described in detail in section \ref{chap:implementation}
The drawback of this is that we have to assign a task leader for this and so the other task might go slower.
In a group, we have already decided that implementing the SD card will be the best use of our time and human resources.
The microprocessor has changed as well as we describe on section\ref{sec:payload controller}.
Therefore, these changes make the whole project much better and more effective.
Every changes in the design means there will be more time spending to recover the task that have been completed. 
Therefore, we could have done the project better if the task was planned at first so there will be no changes in the middle of the project.
Progressive image downloading was the task that was about to implement and we have put many people to look at it. 
It has been proven that it is possible to implement by the MATLAB simulation (section \ref{sec:progressiveimagedisplay}) and also from a lot of research which the team member has been researching(section\ref{jpeg_image_compression}.
Although it seems like a very promising architecture of send the image, the time limitation make this progressive image impossible to implement on the real device.
In the middle of the project, the group meeting has conclude that the progressive image is taking too much of our human resource time and energy.
Therefore, the task has been omitted and there are big reallocation of people to do other tasks.
This might be a big mistake of the group because we have spent a lot of time doing this task.

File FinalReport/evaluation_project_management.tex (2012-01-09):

% This is part of the FinalReport document.
% Copyright (C) 2011 Piyabhum Sornpaisarn, Andrew Busse, Michael Hodgson, John Charlesworth, Paramithi Svastisinha
% See the file COPYING in FinalReport/ for copying conditions.

\section{Evaluation on Project Management (ps)}

In order to successfully meet the specifications of the project, the task needs to be prioritized so that high priority tasks are implemented before the others.
The tasks with high risk, many dependencies, and requiring the most time to complete were the first set of tasks to be completed.
Because we prioritized the tasks well, we had enough time to implement the high priority objectives of the customer's specification.
Although some low priority tasks were completed some tasks such as the progressive image display have been omitted due to time constraints.

The project management took advantage of group meetings. Each members of the group had to produce a formal documentation in order to keep track of and assign the new tasks.
Some meetings did not have enough progress done beforehand and were not as effective as hoped.
If the group agreed to and managed to implement something on every meeting, it would have made the implementation of the project much faster. 

One thing to be learned from this project is the delivery of components which can be very fast or very slow. 
Therefore, before ordering parts, the group would need to check the delivery time and make sure that the delay had a minimal effect on the progress of work.
The hardware arrived on a slightly delayed and so some members of the team who were assigned tasks related to the hardware were forced to reallocate and perform other tasks while waiting for them to be delivered.

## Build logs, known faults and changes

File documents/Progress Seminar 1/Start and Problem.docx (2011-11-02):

# Title Slide:

- Welcome

# Contents Slide:

- Over the next 20 minutes we will:
  - Give a brief description of our project:
    - Problem we have been asked to solve
    - Specification we have reached to solve this problem
  - How we have managed the project so far
  - Our current progress and how this relates to our planned progress
  - And our plans for the future of the project

# Problem Title Slide:

- In order to give you an overview of our project it is important to understand the problems we have been asked to solve

# Problem Slide:

- Main problem is idea of an autopiloted UAV which takes pictures when in the air
  - And stores them on some onboard memory
  - Which is only accessible via physical connection when the aircraft has landed
- Lot of situations where it would be useful to have an idea of what the images are like while we are still in the air
  - We have no idea of quality of images
  - Could be corrupted
  - Camera could not be configured correctly
- We would like to know this before we land the UAV so we can take corrective actions to remedy problem e.g. take more photos
- So it would be very useful for such a UAV to have some method of wirelessly viewing images while it is in the air.

# SkyCircuits Autopilot Slide:

- One such autopilot system where this would be useful is the SkyCircuits autopilot
- Our customer: SkyCircuits, have provided us with an advanced Autopilot module designed to give autopilot capability to a remote control aircraft.
- Lots of very cool features, such as ability to monitor lots of telemetry of aircraft in real-time, autonomously direct the aircraft to GPS waypoints, scripting support and many more
- Notably it also has a wireless link, and allows external ‘payload’ modules to interact and use the wireless link to communicate with a ground station

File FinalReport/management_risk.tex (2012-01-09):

% This is part of the FinalReport document.
% Copyright (C) 2011 Piyabhum Sornpaisarn, Andrew Busse, Michael Hodgson, John Charlesworth, Paramithi Svastisinha
% See the file COPYING in FinalReport/ for copying conditions.

\section{Risk Management (ms)}

A risk assessment was performed at the beginning of the project to make sure that the appropriate actions could be taken when confronted with a problem. 
The following table shows the risks the group has prepared for, the likelihood and 
impact of the risk which determines the priority of the risk, and the appropriate action in response to the risk.

\begin{center}
	\begin{tabular}{ | p{4cm} | p{2cm} | p{2cm} | p{5cm} | }
	\hline
	\textbf{Risk} & \textbf{Likelihood (1: Low, 5: High)} & 
	\textbf{Impact (1: Low, 5: High)} & \textbf{Action} \\ \hline
	Faulty Components & 4 & 4 & Order spares where feasible.
	Source new/replace faulty components as soon as possible otherwise. \\ \hline
	Team member becoming unavailable & 2 & 4 & At least two people per task.
	Reallocating people to different tasks as required. \\ \hline
	Team member facing difficulties & 5 & 2 & At least two people per task.
	Good team communication. Prioritise necessary tasks first. \\ \hline
	Tasks overrunning & 4 & 3 & Plan redundancies into Gantt Charts.
	Reallocate resources when necessary. Communicate between team members often. \\ \hline
	Loss of files/source code & 1 & 5 & Proper use of source control. Back up all source code. \\ \hline
	Loss of access to facilities & 1 & 4 & Work from home laboratory. 
	Buy missing components if necessary \\
	\hline
	\end{tabular}
\end{center}

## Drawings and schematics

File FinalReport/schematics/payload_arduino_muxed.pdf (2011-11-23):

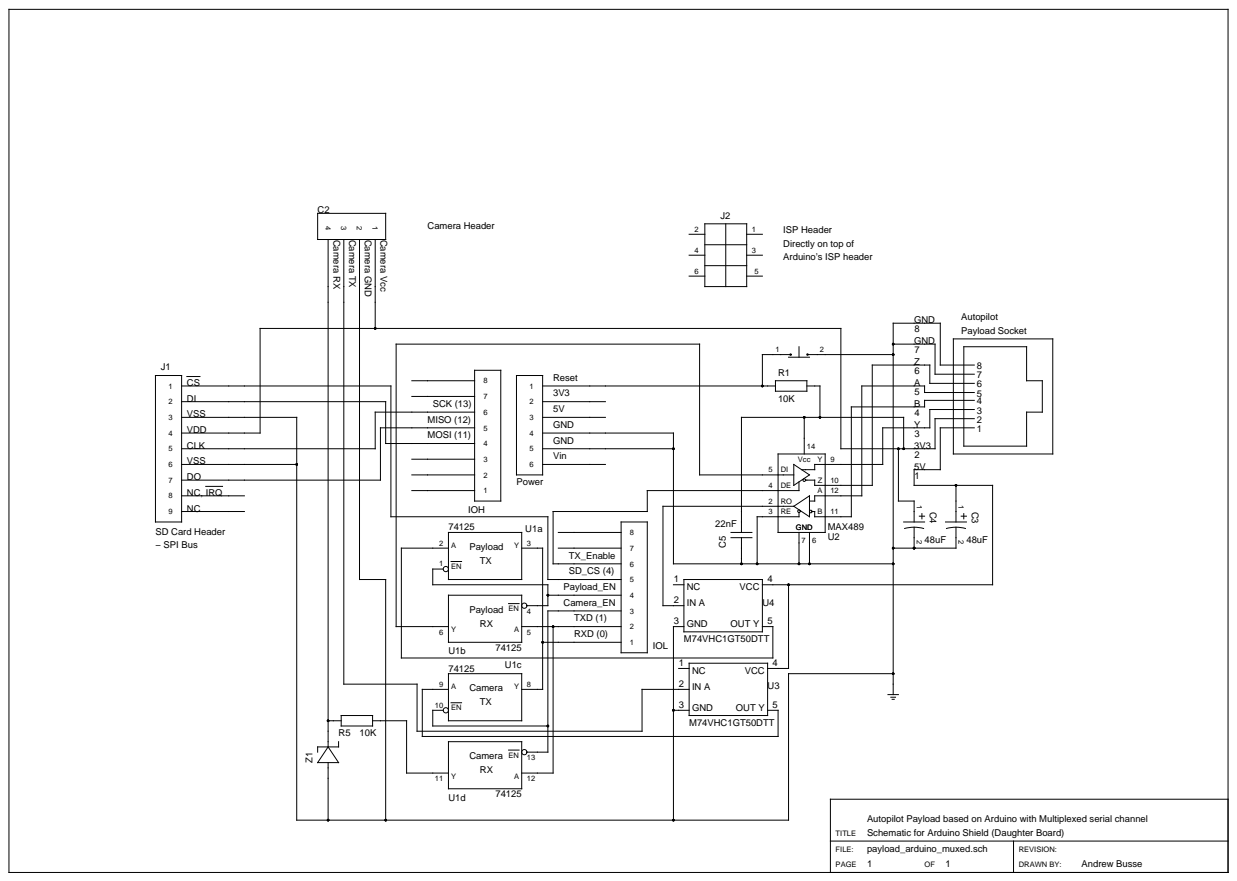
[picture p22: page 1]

ISP Header
Directly on top of
Arduino’s ISP header

VSS
VDD

MISO (12)

Autopilot Payload based on Arduino with Multiplexed serial channel
Schematic for Arduino Shield (Daughter Board)
payload_arduino_muxed.sch

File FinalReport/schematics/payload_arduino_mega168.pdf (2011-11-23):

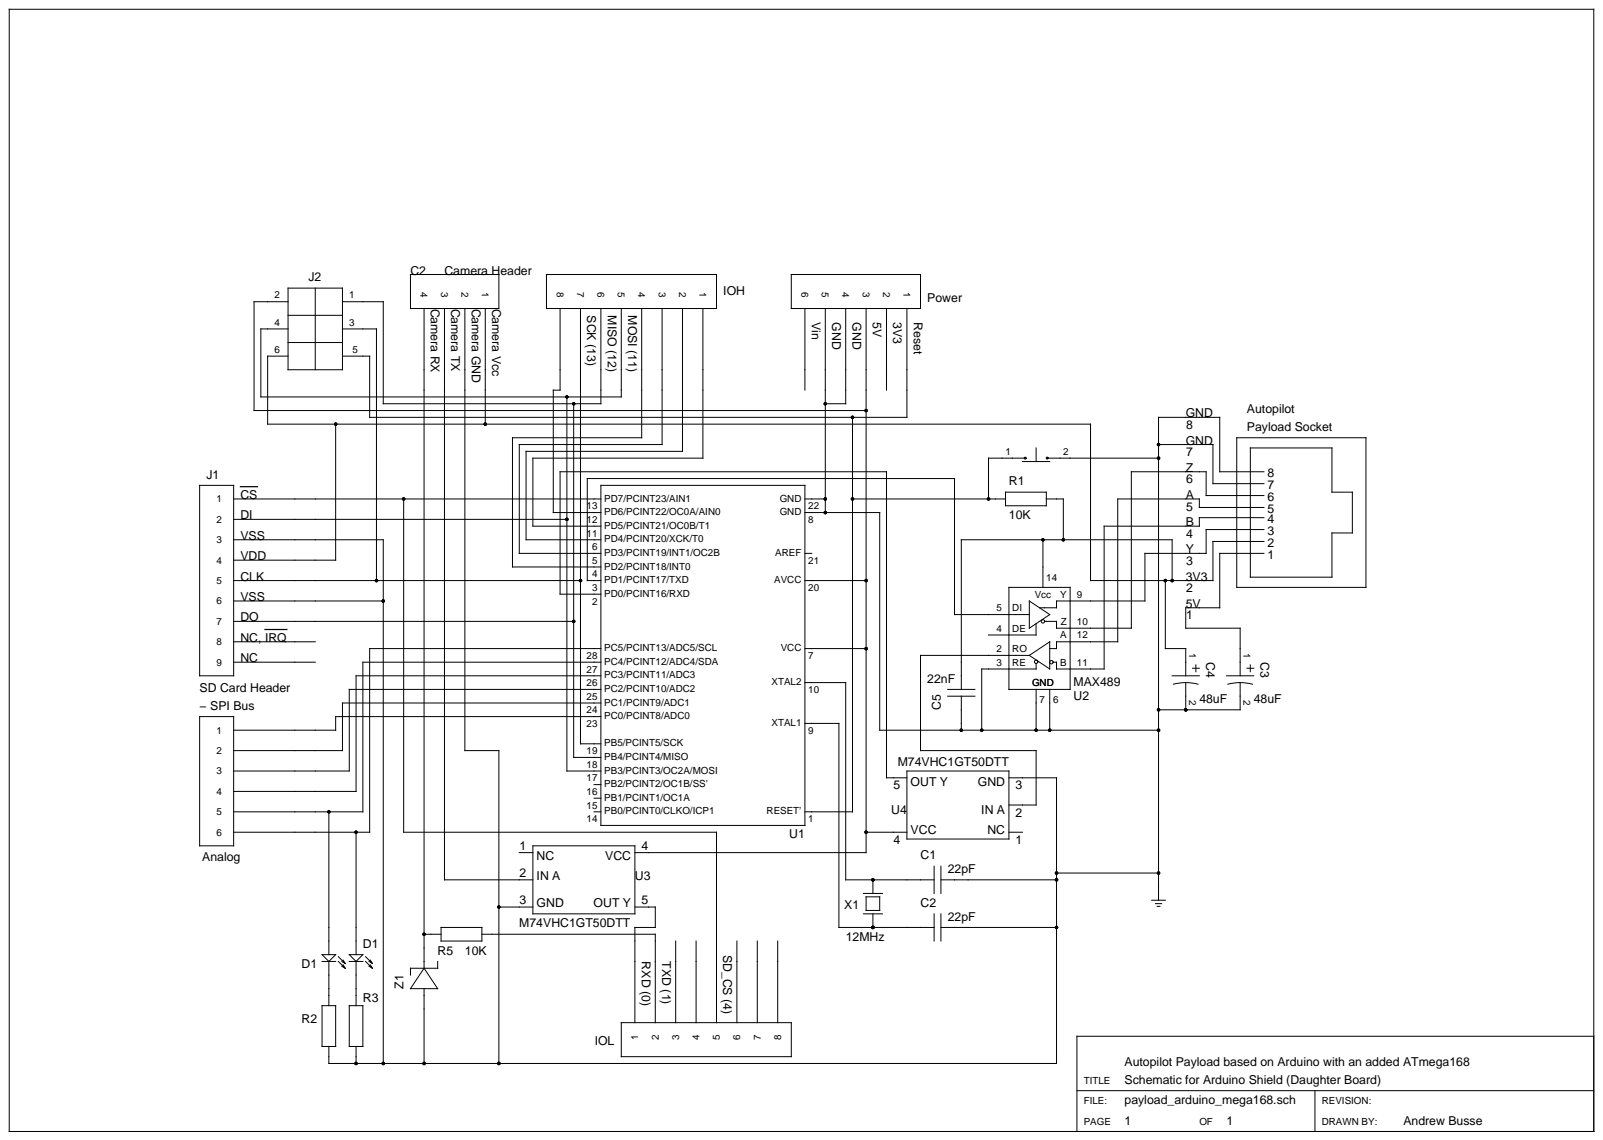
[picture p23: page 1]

VSS

Autopilot Payload based on Arduino with an added ATmega168
Schematic for Arduino Shield (Daughter Board)
payload_arduino_mega168.sch

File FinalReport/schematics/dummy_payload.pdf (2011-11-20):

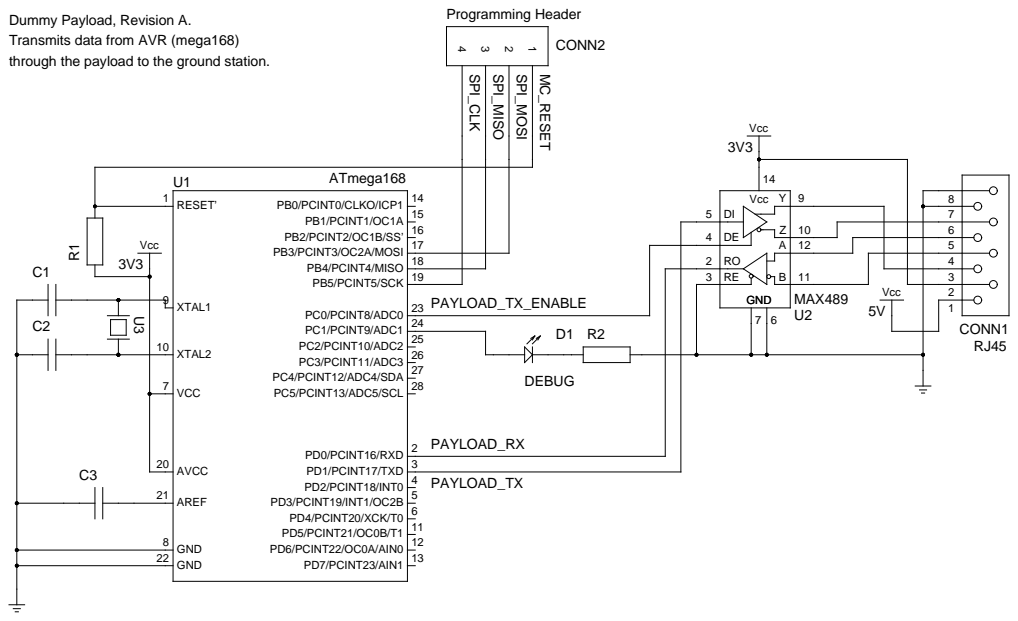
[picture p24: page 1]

Dummy Payload, Revision A.
Transmits data from AVR (mega168)
through the payload to the ground station.

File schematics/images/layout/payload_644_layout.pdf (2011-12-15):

# payload_644.pcb

# 1. Table of Contents (This Page) Created on Thu Dec 15 00:42:42 2011

# 2. component 3. solder 4. plated-drill 5. componentmask 6. soldermask 7. topsilk 8. bottomsilk 9. toppaste 10. topassembly 11. bottomassembly 12. fab

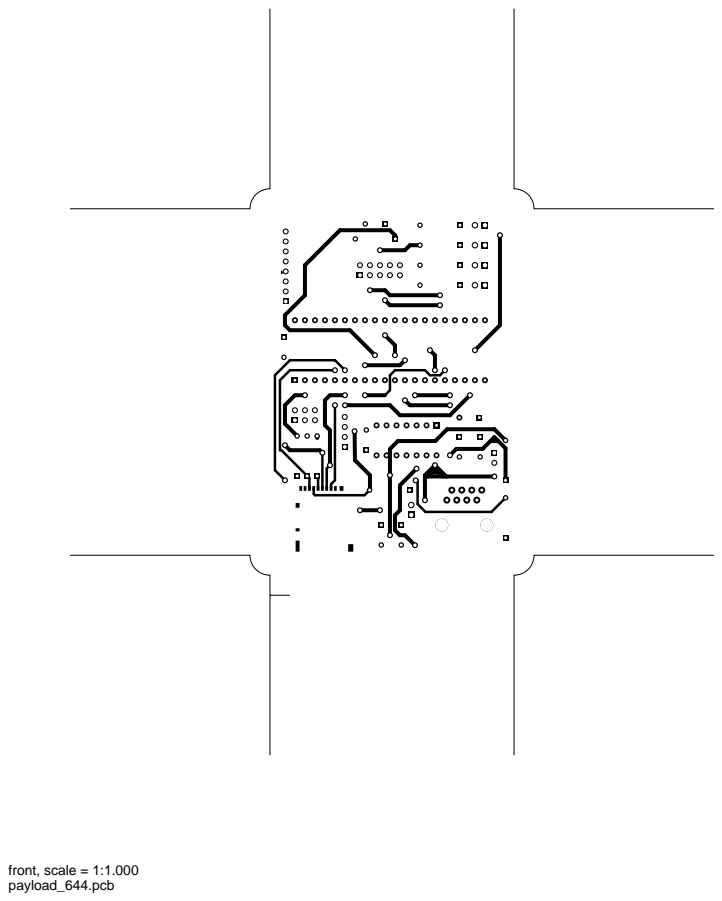
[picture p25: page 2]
front, scale = 1:1.000

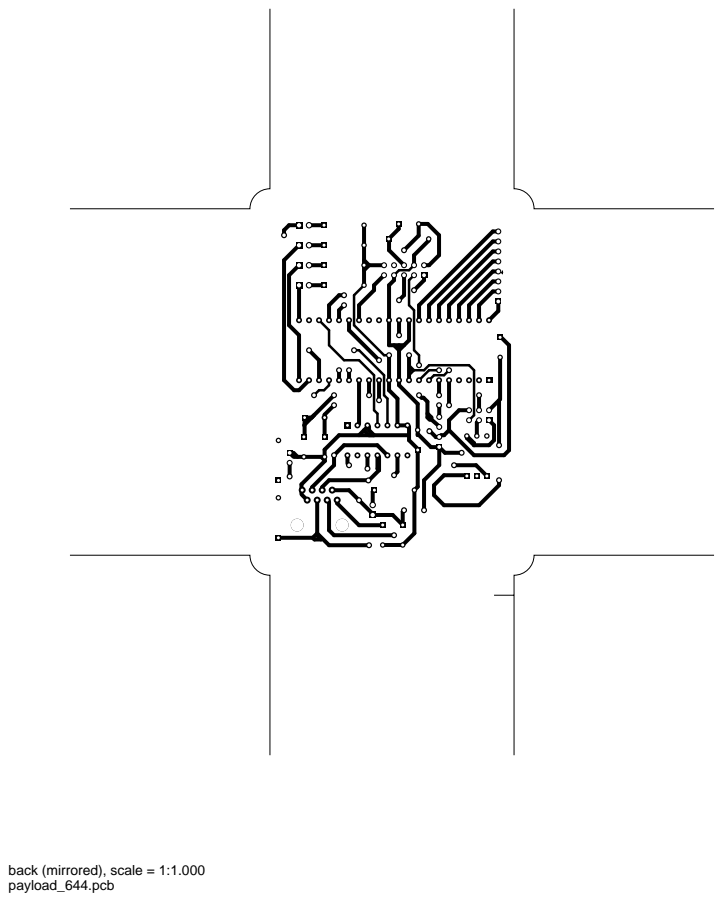
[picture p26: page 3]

back (mirrored), scale = 1:1.000

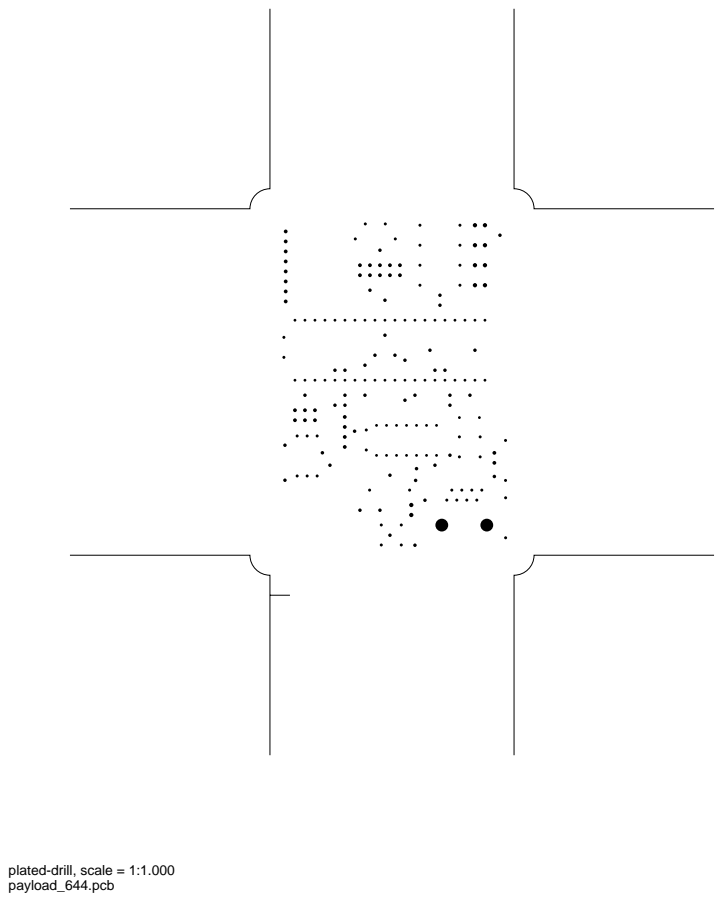
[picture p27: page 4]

plated-drill, scale = 1:1.000

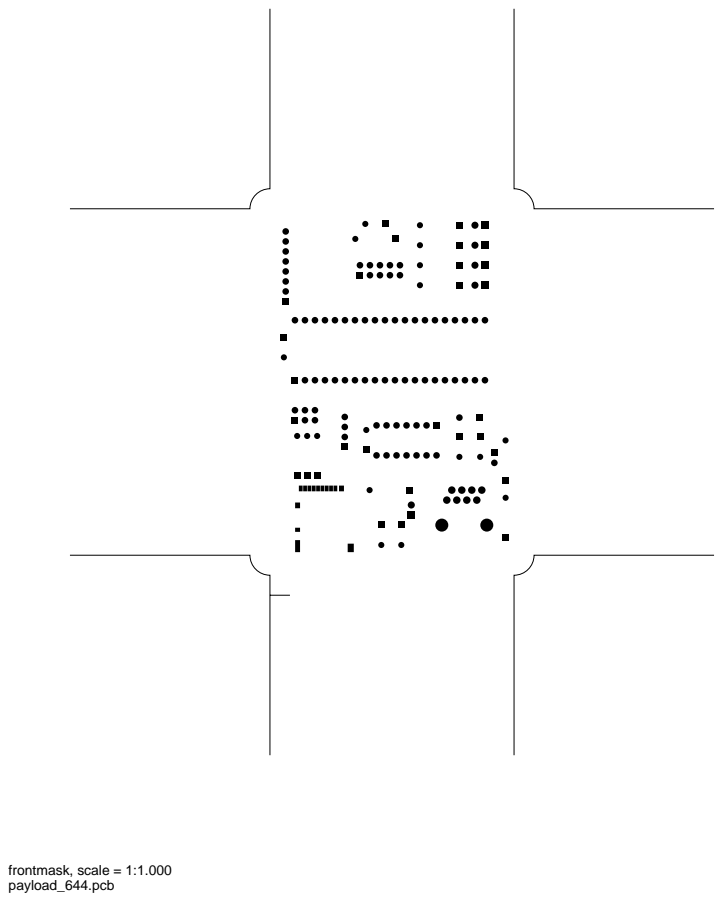
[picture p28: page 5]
frontmask, scale = 1:1.000

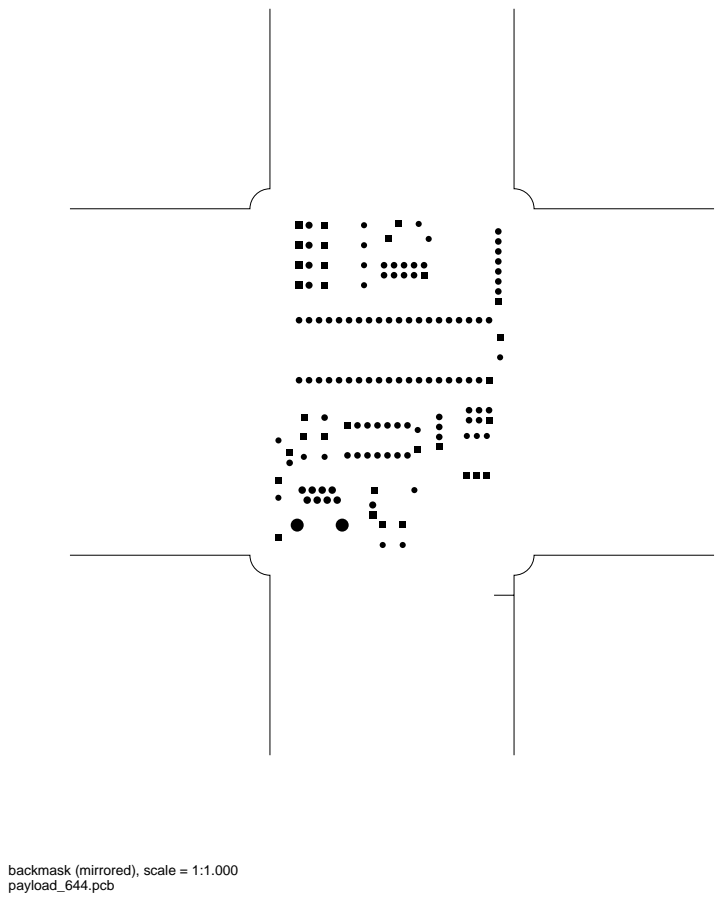
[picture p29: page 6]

backmask (mirrored), scale = 1:1.000

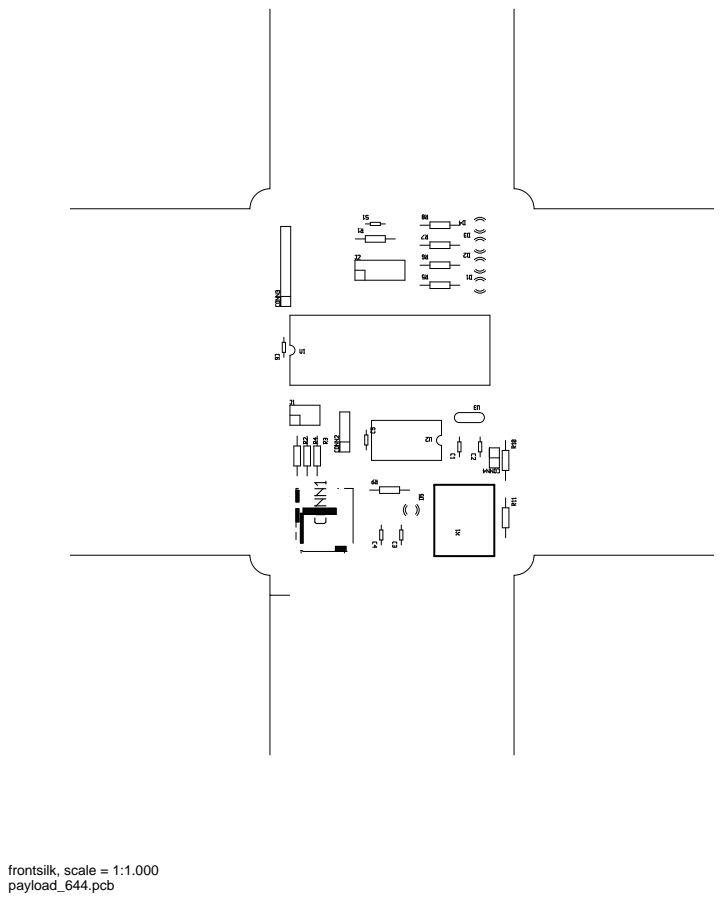
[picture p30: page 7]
frontsilk, scale = 1:1.000

backsilk (mirrored), scale = 1:1.000 frontpaste, scale = 1:1.000

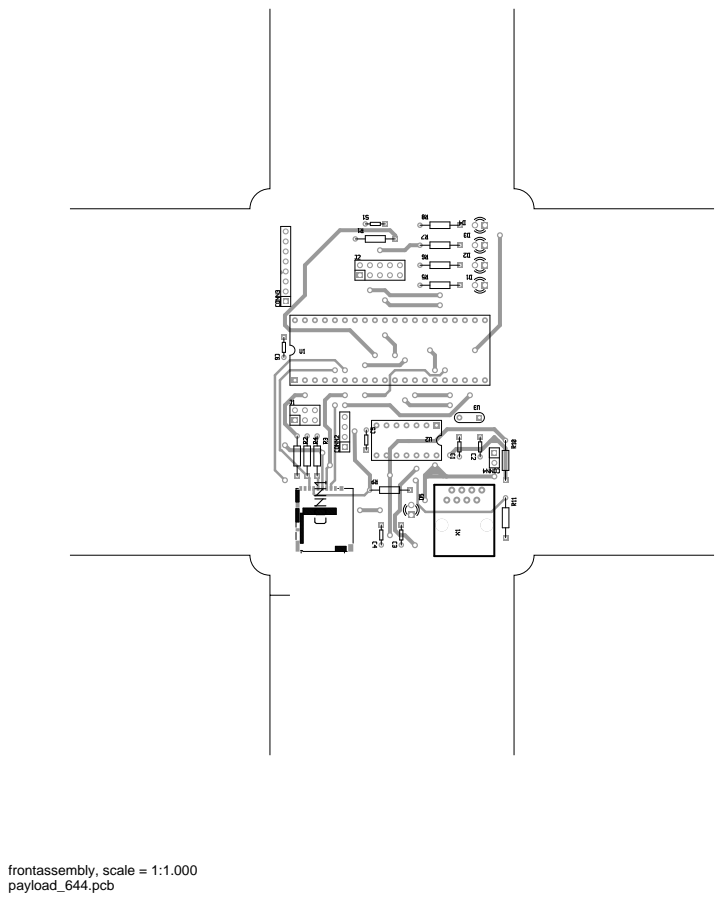
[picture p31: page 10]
frontassembly, scale = 1:1.000

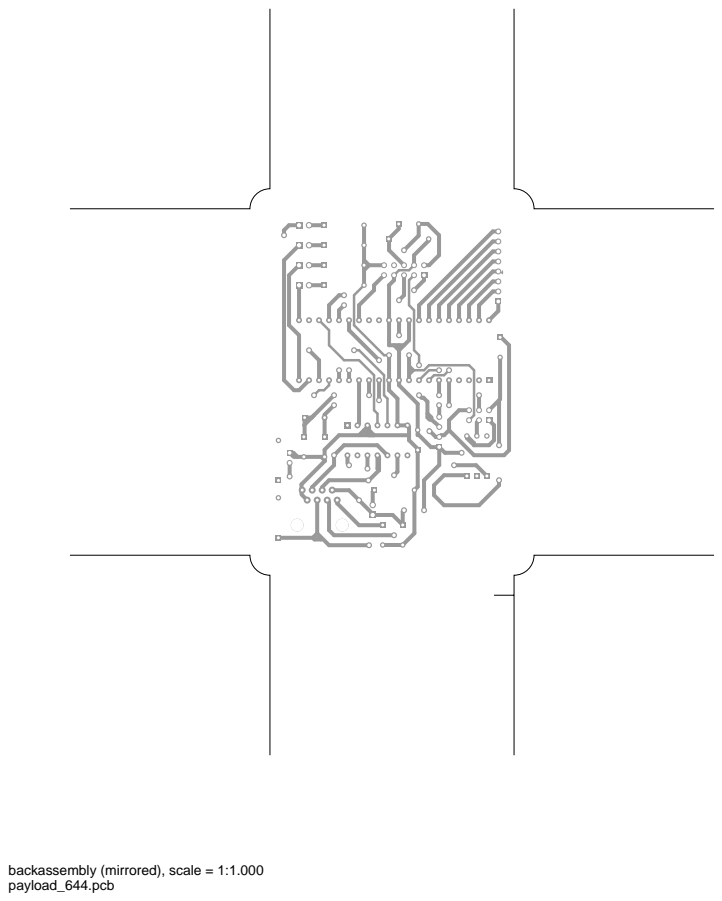
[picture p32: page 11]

backassembly (mirrored), scale = 1:1.000

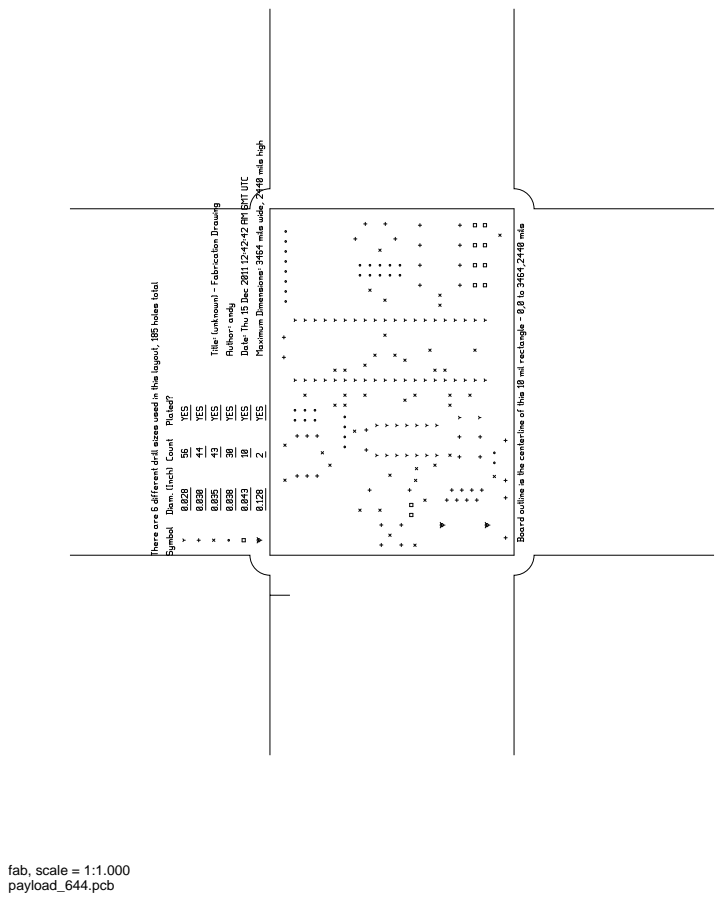
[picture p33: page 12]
fab, scale = 1:1.000

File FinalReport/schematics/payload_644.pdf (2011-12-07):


Autopilot Payload based on ATmega644P processor
payload_644.sch

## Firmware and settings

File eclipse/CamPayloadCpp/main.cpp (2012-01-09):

/* Copyright 2011 Michael Hodgson, Piyabhum Sornpaisarn, Andrew Busse, John Charlesworth, Paramithi Svastisinha

    This file is part of uavcamera.

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
*/

#include "config.h"
#include "spi_debug.h"

#include <avr/io.h>
#include <avr/interrupt.h>
//extern "C" {
#include "mod/base.h"
#include "mod/module.h"
#include "mod/comms.h"
#include "io_pins.h"
//}


#include "camera.h"
#include <WProgram.h>

#include <HardwareSerial.h>

#include "mod/comms.h"
#include "payload_base.h"

#include "SD/SD.h"

#include "mod/uart.h"
#include "image_sender.h"
#include "packet_scan.h"

bool init_sd();



//uint8_t imagePacketToSend[IMAGE_PACKET_SIZE + 3];

int main()
{



	io_pins_setup();

	DDRD |= 0x80;
	PORTD |= 0x80;
	spiDebug.begin();
	module_setup();
	init_image_sender();


	DDRC = 0xFF;
	PORTC = 0x00;

	sei();

	ILOG("Payload starting...");
	ILOG("Initialising SD card...");

	init_sd();

	ILOG("Initialising camera...");

	init_cam();



	DLOG("Entering main loop...");
	while(1) {
		//STATUS_LED_PORT ^= 0x20;
		// main event loop

		/* comms update will process any commands and packet_scan in packet_scan.cpp
		 * will be called to handle any incoming data and messages
		 */
		comms_update();
		/* now the messages have been taken care of we need to process any flags the messages may have set
		 */


		if(imageSendState.sendingImage == true && imageSendState.waitingForAck == true) {
			if(ackReceived && ackCommandID == MID_IMAGE_DATA) {
				imageSendState.waitingForAck = false;
				ackReceived = false;
				//DLOG("Got IMAGE_DATA ACK.\n\r");
			}
		}

		if(imageSendState.sendingImage == true && imageSendState.waitingForAck == true) {

			//if(numTokens > ACK_WAIT_TOKENS || nakReceived == true) {
				if(wait_for_ACK(MID_IMAGE_DATA) == false) {
					if(imageSendState.numRetries > 40) {
						imageSendState.sendingImage = false;
						sdFile.close();
						DLOG("Aborting image send.\n\r");
					} else {
						// we have not got an ack so we need to resend
						if(imageSendState.numPackets < IMAGE_ACK_RESEND_SIZE)
							imageSendState.currentPacket = 0;
						else
							imageSendState.currentPacket = imageSendState.currentPacket - IMAGE_ACK_RESEND_SIZE;

						unsigned long byteNumber = imageSendState.currentPacket * IMAGE_PACKET_SIZE;
						sdFile.seek(byteNumber);
						imageSendState.waitingForAck = false;
						imageSendState.numRetries++;
						DLOG("Resending.\n\r");
					}
				}
			//}
		}

		if(imageSendState.sendingImage == true) {// && imageSendState.waitingForAck == false) {
			//if(imageSendState.currentPacket == 0)
				//DLOG("Starting to send image.\n\r");
			// we are in the middle of sending an image
			// so send the next packet

			if(imageSendState.currentPacket < imageSendState.numPackets) {
				//DLOG("Sending packet ");
				//DLOG(imageSendState.currentPacket);
				//DLOG("\n\r");
				send_IMAGE_DATA_packet();

				if(((imageSendState.currentPacket % IMAGE_ACK_RESEND_SIZE) == 0 && imageSendState.currentPacket != 0) || imageSendState.currentPacket == imageSendState.numPackets) {
					// wait for ack or nak
					imageSendState.waitingForAck = true;
					ackReceived = false;
					nakReceived = false;
					numTokens = 0;
				}
			} else {
				imageSendState.sendingImage = false;
				sdFile.close();
				DLOG("Finished sending image.\n\r");
			}
		}
	}
	return 0;
}

#if 0
int old_main() {
	//init_debug_spi();

	DDRA = 0xFF;

	spiDebug.begin();
	io_pins_setup();
	module_setup();

	init_sd();

	// enable global interrupts
	sei();
	
	// init our camera
	//init_cam();

	// open test1.jpg on the SD card and start reading bytes out of it
	DLOG("Opening jpeg file.\n\r");

	File testJPEGSD = SD.open("TEST1.JPG", FILE_READ);
	if(testJPEGSD == false) {
		DLOG("ERROR: Jpeg file failed to open.\n\r Quitting!\n\r");
		return -1;
	}
	DLOG("Jpeg file opened.\n\r");
	uint32_t testJPEGSDSize = testJPEGSD.size();
	DLOG("TestJPEGDSize: ");
	DLOG("%u", testJPEGSDSize);
	DLOG("\n\r");
	uint16_t numPackets = testJPEGSDSize / IMAGE_PACKET_SIZE;
	if((testJPEGSDSize % IMAGE_PACKET_SIZE) != 0)
		numPackets += 1;
	DLOG("numPackets: ");
	DLOG("%u", numPackets);
	DLOG("\n\r");

	// wait until we start getting tx tokens addressed to us
	DLOG("Waiting for tx token\n\r");
	//while (!recTxToken)
	//	comms_update();
	DLOG("Tx token received\n\r");

	delay(2000);

	DLOG("Starting send\n\r");
/*
	long byteNum = 0;
	int currByte = 0;
	int packetNum = -1;
	do {
		if((byteNum % 20) == 0) {
			packetNum++;
			if(packetNum > 1040) {
				DLOG("\n\r");
				DLOG(packetNum);
				DLOG("# ");
			}
		}

		currByte = testJPEGSD.read();
		if(packetNum > 1040) {
			DLOG(currByte);
			DLOG(" ");
		}
		byteNum++;

	} while(currByte != -1);
*/




	for(uint16_t currPacketNum = 0; currPacketNum < numPackets; currPacketNum++) {
		uint8_t currPacketLength;

		if((currPacketNum == numPackets - 1) && (testJPEGSDSize % IMAGE_PACKET_SIZE != 0)) {
			currPacketLength = testJPEGSDSize % IMAGE_PACKET_SIZE;
			//DLOG("Last packet\n\r");
		} else {
			currPacketLength = IMAGE_PACKET_SIZE;
		}

		currPacketLength += 3;

		//if(currPacketNum > 1140) {
		//	DLOG("#");
		//	DLOG(currPacketNum);
		//	DLOG(": ");
		//}

		imagePacketToSend[0] = currPacketLength - 1;
		imagePacketToSend[1] = (uint8_t)currPacketNum;
		imagePacketToSend[2] = (uint8_t)(currPacketNum >> 8);


		for(int currByteNum = 3; currByteNum < currPacketLength; currByteNum++) {
			uint8_t currByte =	(uint8_t)testJPEGSD.read();
			imagePacketToSend[currByteNum] = currByte;
			//if(currPacketNum > 1140) {
			//	DLOG((int)imagePacketToSend[currByteNum]);
			//	DLOG(" ");
			//}
			if(imagePacketToSend[currByte] == -1) {
				DLOG("ERROR: Trying to read over the end of the file!\n\r");
				return -2;
			}
		}

		//for(int currByteNum = 0; currByteNum < currPacketLength; currByteNum++) {
		//	if(currPacketNum > 1140) {
		//		DLOG((int)imagePacketToSend[currByteNum]);
		//		DLOG(" ");
//			}
//		}

//		if(currPacketNum > 1140) {
//			DLOG("\n\r");
//		}

		//DLOG("Waiting for tx token\n\r");
		//recTxToken = false;
		//while(!recTxToken)
		//	comms_update();
		//DLOG("Got tx token\n\r");
		send_set_class_indexed_item_indexed(CLASS_PAYLOAD, module_id, CLASS_PAYLOAD_MEM_BYTES, 0, imagePacketToSend, currPacketLength);
		//DLOG("Waiting for all data to be transmitted\n\r");
		//DLOG("Class item sent\n\r");
		while(payload_stream.tx_fifo.head != payload_stream.tx_fifo.tail); // spin until all the data has been transmitted
		//DLOG("Transmitted\n\r");
	}


	DLOG("Fin!");

	while(1);
	// now we have got at least one tx token so we know we are connected and ready to send stuff


	uint32_t numBytesTrans = 0;


	for(uint16_t currPacketNum = 0; currPacketNum < numPackets; currPacketNum++) {
		//DLOG("Sending data\n\r");
		// wait for the next tx token
		//DLOG("Sending packet #");
		//DLOG(currPacketNum);
		//DLOG("\n\r");

		uint8_t currPacketSize = IMAGE_PACKET_SIZE;
		/*if((uint32_t)((uint32_t)currPacketNum * (uint32_t)IMAGE_PACKET_SIZE) > testJPEGSDSize) {
			// if we are at the end of the image and we don't want to send all IMAGE_PACKET_SIZE bytes
			currPacketSize = (uint32_t)IMAGE_PACKET_SIZE - ((uint32_t)((uint32_t)currPacketNum * (uint32_t)IMAGE_PACKET_SIZE) - testJPEGSDSize);
			DLOG("Last packet\n\r");
		}*/

		if(currPacketNum == numPackets - 1) {
			currPacketSize = testJPEGSDSize % IMAGE_PACKET_SIZE;
			//DLOG("Last packet\n\r");
		}
		currPacketSize += 2; // take into account the current packet number

		//DLOG("Current package size: ");
		//DLOG((int)currPacketSize);
		//DLOG("\n\r");

		imagePacketToSend[0] = currPacketSize;

		imagePacketToSend[1] = (uint8_t)currPacketNum;
		imagePacketToSend[2] = (uint8_t)(currPacketNum >> 8);
		for(int currByte = 3; currByte < currPacketSize + 3; currByte++) {
			imagePacketToSend[currByte] = (uint8_t)testJPEGSD.read();
			numBytesTrans++;
			if(imagePacketToSend[currByte] == -1) {
				DLOG("ERROR: Trying to read over the end of the file!\n\r");
				return -2;
			}
		}

		while(uart0_tx_idle == FALSE) {
					comms_update();
		}

		//DLOG("Waiting for tx token\n\r");
		//recTxToken = false;
		//while(!recTxToken)
		//	comms_update();
		//DLOG("Got tx token\n\r");
		PORTA = 0x00;
		PORTA = 0xFF;
		PORTA = 0x00;
		send_set_class_indexed_item_indexed(CLASS_PAYLOAD, module_id, CLASS_PAYLOAD_MEM_BYTES, 0, imagePacketToSend, currPacketSize + 1);
		PORTA = 0xFF;
		//DLOG("Waiting for all data to be transmitted\n\r");
		//DLOG("Class item sent\n\r");
		while(payload_stream.tx_fifo.head != payload_stream.tx_fifo.tail); // spin until all the data has been transmitted
		//DLOG("Transmitted\n\r");
		PORTA = 0x00;

	}

	DLOG("numBytesTrans: ");
	DLOG("%u", numBytesTrans);
	DLOG("\n\r");

	DLOG("Finished!\n\r");

	// take a single image
	//take_picture();

	return (0);
}
#endif

bool init_sd() {
	// Pin 10 = Chip Select
	pinMode(10, OUTPUT);

	// If SD not connected, stop execution
	if (!SD.begin()) {
		DLOG("SD Failed\n\r");
		return false;
	}
		DLOG("SD Working\n\r");
		return true;
}

/*int dSPIMOSIPin = 12;
int dSPISCLKPin = 13;
int dSPISS = 14;
*/
void init_debug_spi() {

}

void send_debug_spi(char* string) {
	/*digitalWrite(dSPISS, LOW);
	delayMicroseconds(100);
	int i = 0;
	while(string[i] != '\0') {
		for(int j = 0; j < 8; j++) {
			if((string[i] & (0x01 << j)) >> j)
				digitalWrite(dSPIMOSIPin, LOW);
			else
				digitalWrite(dSPIMOSIPin, HIGH);

			digitalWrite(dSPISCLKPin, LOW);
			delayMicroseconds(100);
			digitalWrite(dSPISCLKPin, HIGH);
			delayMicroseconds(100);
		}
		i++;
	}
	digitalWrite(dSPISS, HIGH);*/

	spiDebug.print(string);
}

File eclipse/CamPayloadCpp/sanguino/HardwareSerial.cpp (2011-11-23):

/*
  HardwareSerial.cpp - Hardware serial library for Wiring
  Copyright (c) 2006 Nicholas Zambetti.  All right reserved.

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
  Modified 23 November 2006 by David A. Mellis
*/

#include "../config.h"

#include <stdio.h>
#include <string.h>
#include <inttypes.h>
#include "wiring.h"
#include "wiring_private.h"

#include "HardwareSerial.h"

// Define constants and variables for buffering incoming serial data.  We're
// using a ring buffer (I think), in which rx_buffer_head is the index of the
// location to which to write the next incoming character and rx_buffer_tail
// is the index of the location from which to read.
#define RX_BUFFER_SIZE 128

struct ring_buffer {
  unsigned char buffer[RX_BUFFER_SIZE];
  int head;
  int tail;
};

ring_buffer rx_buffer = { { 0 }, 0, 0 };

#if defined(__AVR_ATmega644P__) || defined(__AVR_ATmega1280__)
ring_buffer rx_buffer1 = { { 0 }, 0, 0 };
#endif

#if defined(__AVR_ATmega1280__)
ring_buffer rx_buffer2 = { { 0 }, 0, 0 };
ring_buffer rx_buffer3 = { { 0 }, 0, 0 };
#endif

inline void store_char(unsigned char c, ring_buffer *rx_buffer)
{
  int i = (rx_buffer->head + 1) % RX_BUFFER_SIZE;

  // if we should be storing the received character into the location
  // just before the tail (meaning that the head would advance to the
  // current location of the tail), we're about to overflow the buffer
  // and so we don't write the character or advance the head.
  if (i != rx_buffer->tail) {
    rx_buffer->buffer[rx_buffer->head] = c;
    rx_buffer->head = i;
  }
}

#if defined(__AVR_ATmega644P__) || defined(__AVR_ATmega1280__)
#ifndef CUSTOM_UART_0
ISR(USART0_RX_vect)
{
  unsigned char c = UDR0;
  store_char(c, &rx_buffer);
}
#endif

ISR(USART1_RX_vect)
{
  unsigned char c = UDR1;
  store_char(c, &rx_buffer1);
}

#if defined(__AVR_ATmega1280__)
ISR(USART2_RX_vect)
{
  unsigned char c = UDR2;
  store_char(c, &rx_buffer2);
}

ISR(USART3_RX_vect)
{
  unsigned char c = UDR3;
  store_char(c, &rx_buffer3);
}
#endif

#else

#if defined(__AVR_ATmega8__)
SIGNAL(SIG_UART_RECV)
#else
SIGNAL(USART_RX_vect)
#endif
{
#if defined(__AVR_ATmega8__)
  unsigned char c = UDR;
#else
  unsigned char c = UDR0;
#endif
  store_char(c, &rx_buffer);
}

#endif

// Constructors ////////////////////////////////////////////////////////////////

HardwareSerial::HardwareSerial(ring_buffer *rx_buffer,
  volatile uint8_t *ubrrh, volatile uint8_t *ubrrl,
  volatile uint8_t *ucsra, volatile uint8_t *ucsrb,
  volatile uint8_t *udr,
  uint8_t rxen, uint8_t txen, uint8_t rxcie, uint8_t udre, uint8_t u2x)
{
  _rx_buffer = rx_buffer;
  _ubrrh = ubrrh;
  _ubrrl = ubrrl;
  _ucsra = ucsra;
  _ucsrb = ucsrb;
  _udr = udr;
  _rxen = rxen;
  _txen = txen;
  _rxcie = rxcie;
  _udre = udre;
  _u2x = u2x;
}

// Public Methods //////////////////////////////////////////////////////////////

void HardwareSerial::begin(long baud)
{
  uint16_t baud_setting;
  bool use_u2x;

  // U2X mode is needed for baud rates higher than (CPU Hz / 16)
  if (baud > F_CPU / 16) {
    use_u2x = true;
  } else {
    // figure out if U2X mode would allow for a better connection
    
    // calculate the percent difference between the baud-rate specified and
    // the real baud rate for both U2X and non-U2X mode (0-255 error percent)
    uint8_t nonu2x_baud_error = abs((int)(255-((F_CPU/(16*(((F_CPU/8/baud-1)/2)+1))*255)/baud)));
    uint8_t u2x_baud_error = abs((int)(255-((F_CPU/(8*(((F_CPU/4/baud-1)/2)+1))*255)/baud)));
    
    // prefer non-U2X mode because it handles clock skew better
    use_u2x = (nonu2x_baud_error > u2x_baud_error);
  }
  
  if (use_u2x) {
    *_ucsra = 1 << _u2x;
    baud_setting = (F_CPU / 4 / baud - 1) / 2;
  } else {
    *_ucsra = 0;
    baud_setting = (F_CPU / 8 / baud - 1) / 2;
  }

  // assign the baud_setting, a.k.a. ubbr (USART Baud Rate Register)
  *_ubrrh = baud_setting >> 8;
  *_ubrrl = baud_setting;

  sbi(*_ucsrb, _rxen);
  sbi(*_ucsrb, _txen);
  sbi(*_ucsrb, _rxcie);
}

void HardwareSerial::end()
{
  cbi(*_ucsrb, _rxen);
  cbi(*_ucsrb, _txen);
  cbi(*_ucsrb, _rxcie);  
}

uint8_t HardwareSerial::available(void)
{
  return (RX_BUFFER_SIZE + _rx_buffer->head - _rx_buffer->tail) % RX_BUFFER_SIZE;
}

int HardwareSerial::read(void)
{
  // if the head isn't ahead of the tail, we don't have any characters
  if (_rx_buffer->head == _rx_buffer->tail) {
    return -1;
  } else {
    unsigned char c = _rx_buffer->buffer[_rx_buffer->tail];
    _rx_buffer->tail = (_rx_buffer->tail + 1) % RX_BUFFER_SIZE;
    return c;
  }
}
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

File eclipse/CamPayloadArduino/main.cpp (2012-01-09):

/* Copyright 2011 Michael Hodgson, Piyabhum Sornpaisarn, Andrew Busse, John Charlesworth, Paramithi Svastisinha

    This file is part of uavcamera.

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
*/

#include <WProgram.h>

// Camera -> SD Card Code

// PIN LAYOUT:
// Digital 13  <->  SD CLK
// Digital 12  <->  SD MISO / Data 0 / SO
// Digital 11  <->  SD MOSI / CMD / DI
// Digital 4   <->  SD D3
// Arduino RX  <->  Camera TX
// Arduino TX  <->  Camera RX

#include "SoftwareSerial/SoftwareSerial.h"
#include "SD/SD.h"
#include <stdio.h>

#define DLOG(...)  sSerial.print(__VA_ARGS__)
//#define DLOG(...)
byte SYNC[] = {0xAA,0x0D,0x00,0x00,0x00,0x00};
byte RXtest[6];

// Serial PC cable to view error messages
#define sRxPin 2
#define sTxPin 3

SoftwareSerial sSerial = SoftwareSerial(sRxPin, sTxPin);
char filePrefix[] = "test"; //Prefix of file name written to the SD card
char fileExt[] = ".jpg"; //File extension of the file being written to
char fileName[13]; //Contains full file name of file being written to
char numBuf[5]; //Number buffer, for the "find a file that doesn't exist" procedure. Could be a number up to 32767
File jpgFile;

// The following are all self-explanatory.
// Follows command structure described in the camera's datasheet

// sends commands to the camera
void sendCommand(byte ID1, byte ID2, byte par1, byte par2, byte par3, byte par4) {
  byte Command[] = {ID1,ID2,par1,par2,par3,par4};
  Serial.write(Command, 6);
}

// receives messages from the camera
void receiveComd() {
  for(int z = 0;z<6;z++){
      while (Serial.available() <= 0) {}
      RXtest[z] = Serial.read();
  }
}

void sendSYNC() {
  sendCommand(0xAA,0x0D,0x00,0x00,0x00,0x00);
}

void sendACK(byte comID, byte ACKcounter, byte pakID1, byte pakID2) {
 sendCommand(0xAA,0x0E,comID,ACKcounter,pakID1,pakID2);
}

void sendINITIAL(byte colourType, byte rawRes, byte jpegRes) {
 sendCommand(0xAA,0x01,0x00,colourType,rawRes,jpegRes);
}

void sendSETPACKAGESIZE(byte paklb, byte pakhb) {
 sendCommand(0xAA,0x06,0x08,paklb,pakhb,0x00);
}

void sendSNAPSHOT(byte snapType, byte skip1, byte skip2) {
 sendCommand(0xAA,0x05,snapType,skip1,skip2,0x00);
}

void sendGETPICTURE(byte picType) {
 sendCommand(0xAA,0x04,picType,0x00,0x00,0x00);
}



// verifies ACK
boolean isACK(byte byteundertest[],byte comID, byte pakID1, byte pakID2){
  byte testACK[] = {0xAA,0x0E,comID,0x00,pakID1,pakID2};
  for(int z = 0;z<6;z++){
    if((z != 3) && (byteundertest[z] != testACK[z]))
      return false;
  }
  return true;
}

// verifies SYNC
boolean isSYNC(byte byteundertest[]){
  for(int z = 0;z<6;z++){
    if(byteundertest[z] != SYNC[z])
      return false;
  }
  return true;
}

// verifies DATA
boolean isDATA(byte byteundertest[]){
    if((byteundertest[0] != 0xAA) || (byteundertest[1] != 0x0A)){
      return false; }
  return true;
}

// setup the file on the sd card

void setupSD(char fileName[]){
  // For Optimisation of the SD card writing process.
  // See http://www.arduino.cc/cgi-bin/yabb2/YaBB.pl?num=1293975555
  jpgFile = SD.open(fileName, O_CREAT | O_WRITE);
}

// synchronise with camera
void establishContact() {
  DLOG("Sending syncs\n\r\r"); // Send SYNC to the camera.
  //This could be up to 60 times
  while(1){
    while (Serial.available() <= 0) {
      DLOG(".");
      sendSYNC();
      delay(50);
    }

    receiveComd();
 // Verify that the camera has sent back an ACK followed by SYNC
    if(!isACK(RXtest,0x0D,0x00,0x00))
      continue;
    DLOG("ACK received\n\r");
    receiveComd();

   if(!isSYNC(RXtest))
     continue;

   DLOG("SYNC received\n\r");
   // Send back an ACK
   sendACK(0x0D,0x00,0x00,0x00);

   break;
  }
}

// takes a snapshot
boolean takeSnapshot() {

  // setup image parameters
  DLOG("sending initial\n\r");
  delay(50);
  sendINITIAL(0x07,0x07,0x07);
  receiveComd();
  if(!isACK(RXtest,0x01,0x00,0x00))
      return false;
  DLOG("ACK received\n\r");

  // Package size = maximum of 512 bytes
  // Arduino serial.read() buffer size = 128 bytes
  unsigned int packageSize = 64;

  // sets the size of the packets to be sent from the camera
  DLOG("sending setpackagesize\n\r");
  delay(50);
  sendSETPACKAGESIZE((byte)packageSize,(byte)(packageSize>>8));
  receiveComd();
  if(!isACK(RXtest,0x06,0x00,0x00))
      return false;
  DLOG("ACK received\r");

  // camera stores a single frame in its buffer
  DLOG("sending snapshot\n\r");
  delay(50);
  sendSNAPSHOT(0x00,0x00,0x00);
  receiveComd();
  if(!isACK(RXtest,0x05,0x00,0x00))
      return false;
  DLOG("ACK received\n\r");

  // requests the image from the camera
  DLOG("sending getpicture\n\r");
  delay(50);
  sendGETPICTURE(0x01);
  receiveComd();
  if(!isACK(RXtest,0x04,0x00,0x00))
      return false;
  DLOG("ACK received\n\r");
  receiveComd();
  if(!isDATA(RXtest))
      return false;
  DLOG("DATA received\n\r");

  // Strips out the "number of packages" from the DATA command
  // then displays this over the serial link
  unsigned long bufferSize = 0;
  bufferSize = RXtest[5] | bufferSize;
  bufferSize = (bufferSize<<8) | RXtest[4];
  bufferSize = (bufferSize<<8) | RXtest[3];

  unsigned int numPackages = bufferSize/(packageSize-6);

  DLOG("Number of packages: ");
  DLOG(numPackages,DEC);
  sSerial.println();

  byte dataIn[packageSize];
  int flushCount = 0;

  for(unsigned int package = 0;package<numPackages;package++){

    //DLOG("Sending ACK for package ");
    //DLOG(package,DEC);
    //DLOG("\n\r");
    sendACK(0x00,0x00,(byte)package,(byte)(package>>8));

      // receive package
      for(int dataPoint = 0; dataPoint<packageSize;dataPoint++){
        while (Serial.available() <= 0) {} // wait for data to be available n.b. will wait forever...
        dataIn[dataPoint] = Serial.read();
          if(dataPoint > 3 && dataPoint < (packageSize - 2)){ //strips out header data
          //sSerial.print(dataIn[dataPoint],BYTE);
          jpgFile.print(dataIn[dataPoint]);
            if(flushCount == 511){
              jpgFile.flush();
              flushCount = -1; // because it adds one straight away after
            }
          flushCount++;
          }
        //DLOG(dataPoint);
        //DLOG("\n\r");
      }
    //DLOG("Package ");
    //DLOG(package);
    //DLOG(" read successfully\n\r");

  }

  sendACK(0x0A,0x00,0xF0,0xF0);
  DLOG("Final ACK sent\n\r");
  return true;
}



void setup()
{
  // start serial port at 115200 bps
  Serial.begin(115200);
  sSerial.begin(9600);

  // start software serial library for debugging
  pinMode(sRxPin, INPUT);
  pinMode(sTxPin, OUTPUT);
  // Pin 10 = Chip Select
  pinMode(10, OUTPUT);

  // If SD not connected, stop execution
  if (!SD.begin(4)) {
    DLOG("SD Failed");
    return;
  }
  DLOG("SD Working");

  //DLOG("Attemting to establish contact.\n\r");
  establishContact();  // send a byte to establish contact until receiver responds
  //DLOG("Contact established, captain\n\r");
  delay(2000); // 2 second pause


}
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

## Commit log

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2011-10-06 Spec version 2 created.
    Added:
    * deliverable repository added for the customer at the end
    * created middle incomplete paragraph containing all the criteria
    Not yet added:
    * Block diagram
    * PCB considerations
    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
2011-10-14 Added in debug code for camera capture - camera now transmits debug info on a separate serial connection
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2011-10-31 This new commit update peak_test.c and peak_test.h. You should change only these files. Because his code works already. peak_test_send_int use to send a stream of int peak_test.h define #define CLASS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
    [main.c]
2011-10-31 sorry the file earlier has an error so it's fine now
    [main.c]
2011-10-31 Update README to track recent additions to the repository.
    Left a couple of lines blank for Peak/Mitch to update, as they understand
    what's going on in those two folders a lot better than I do.
2011-11-05 Add schematic for dummy payload as it currently exists. Values to follow tomorrow.
    Instructions on how to use schematic, plus a JPG for those who don't want to install
    the software, is to follow shortly.
    [dummy_payload.sch]
2011-11-05 Add jpeg image of the dummy payload schematic
    Makes things viewable for people who can't use gEDA
2011-11-05 Remove unnecessary files from sample payload code.
    Having these made the makefile process b0rk when running "$ make" in Fedora 15
    Removing them made it work again
    Theoretically, these are not needed, as when you run "$make all", all of the files
    I'm now deleting are re-generated. Besides, you're almost certainly going to need
    to rebuild these to reflect a change to the makefile (different programmer, AVR, etc.)
2011-11-07 the Connector.cs have been updated to check the start of file with bool isStartOfFile and can check the end using endOfFile However this program can still test with any kind of data. There is a line 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
2011-11-08 - attempting to get my huffman code to work with arduino code - managed to get arduino C++ and huffman code to compile together
2011-11-09 gettingJPEGdataInC is a program that can read data from the camera and convert in to Table which we can understand. The completed header are: APP0 SOI EOI DQT APPn
    the uncompleted header are:
    DHT
    SOS
    We will need to test this with the real image data later after all the header finished
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2011-11-14 Fix up comments in camera->SD arduino code
    [cameraSD_pde.pde]
2011-11-14 Add feature that ensures existing .jpg are not overwritten
    Note that this is, as yet, untested on our prototype.
    Might need to investigate stripping out snprintf() and replacing
    with itoa() -> arduino website suggests this might save us over 1.5kB
    of program memory
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2011-11-20 Create a schematics directory
    This is about to contain a few more schematics. Hold on to your hats...
    [dummy_payload.sch]
2011-11-20 Add some symbols for the impending schematics
    ATmega644P-dip is modified from:
    http://www.gedasymbols.org/user/anton_dubniak/symbols/MCU/ATmega644.sym
    (modifications made with reference to datasheet linked to, for the PDIP chip)
    modular_8p8c is directly copied from:
    http://www.gedasymbols.org/user/alexander_kurz/symbols/modular_8p8c.sym
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2011-11-20 Invert pin numbering to match JTAG/ISP header pin numbering scheme
    Taken from Steve Gunn's Il Matto schematics
2011-11-20 - have been debugging code for programAVR to get the autopilot to work - added eclipse projects for arduino code - added current port of the payload sofware to the ATMega644P in CamPayloadCpp, have a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
    [TcfTransactionLog.csv]
2011-11-20 Swap some pin numbers on the 10-way header. Oops.
    Repeated pin 3 where pin 1 should be. This is now fixed.
2011-11-20 Add schematic for a payload based on an ATmega644P
    Some influence from the design of the Il Matto (designed by Steve Gunn
    for last year's D4 labs). Lacks expansion headers present on the Il
    Matto, these may be added at a later date.
    [payload_644.sch]
2011-11-20 - fixed some compiler errors referring to double references because wiring_serial.c was defining things again
    [main.cpp, wiring_serial.c]
2011-11-20 - fixed an undefined reference to vtable error in Print.h by setting a virtual function = 0 - added pure_virtual.cpp to fix problem referring to __cxa_pure_virtual
2011-11-20 Add a border to payload schematic
    [payload_644.sch]
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2011-11-22 Add schematic for a payload which multiplexes the arduino's serial channel
    Multiplexing achieved with tri-state buffers. Would have been done with
    a 2:1 mux and 1:2 demux, but there isn't a single package which does
    this nicely for us. Tri-states can be done on a single chip, saving
    quite a lot of board space
    [payload_arduino_muxed.sch]
2011-11-22 Schematic for a payload with arduino + daughter board containing ATmega168
    The idea being, no need to multiplex a single serial channel, we could use
    arduino to do camera -> SD card, and '168 to do SD card -> autopilot ->
    ground station
    [payload_arduino_mega168.sch]
2011-11-22 payload_644 will be actual schematic, start adding footprints + uSD
    SD -> microSD card. Smaller footprint, slightly easier to solder. Can't
    find an existing component symbol for the microSD, so I'm using a standard
    8-way connector in its place for the time being. As long as the relevant
    footprint is attached, gschem2pcb shouldn't care.
    [payload_644.sch]
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2011-11-22 Fix header6-2.sym, and the schematics that use it.
    [payload_644.sch, payload_arduino_mega168.sch, payload_arduino_muxed.sch]
2011-11-23 Add footprints to schematic ready for conversion to PCB
    [payload_644.sch]
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2011-11-23 Generate images of arduino+ATmega168 schematic
    For those who can't/won't use gEDA.
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2011-11-23 Add external power connection, transceiver resistors to schematic+pcb
    [payload_644.sch]
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2011-11-23 modified and added lots of stuff while the svn was down basically the basic system works now, the take picture code works and the send stuff to autopilot code works also
    - hacked sanguino stuff into working
    - fixed bug in mod/uart.c where the tx_enable pin was not being set low at
    the correct time since it was being set in the tx buffer ready interrupt
    which is called before it should be set low. fixed by enabling tx finished
    interrupt and setting it there
    - added arduino SD card stuff and hacked into working with sanguino code
    - made everything C++ by renaming all c files to cpp files and modifying a
    few casts etc
    - added in spi_debug to allow debug text to be sent over bitbanged spi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
    [HardwareSerial.cpp, SoftwareSerial.cpp, camera.cpp]
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2011-11-24 - got image data sending working, it does not conform to the proper packet structure yet (no IMAGE_DATA message id at the beginning) but that should not take too long to fix
    - BUT it is sending at pretty much full speed (perhaps we can squeese a few
    more bytes per package out of it) Meaning download speeds of under 10
    seconds for a full size test image!
    - while getting it to work with the new code structure I ran into an
    incredibly annoying and difficult to debug bug, basically a while loop was
    testing on a variable which was being changed externally to the loop, but
    for some reason this was not picked up by the while loop so it would never
    exit (probably because the test cond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
    [camera.cpp, comms.h, main.cpp]
2011-11-25 - added peaks gui to NCamGS - we can now use it to take a picture and display it on the screen - still a few bugs: - can only take pictures once since for some reason it says output.jpg is still in u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
2011-11-25 added some debug code to find out why the camera only works every other time, still not solved
    [camera.cpp, main.cpp]
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2011-11-28 - finally made the system work properly, now all implemented features of the payload seem to be working correctly - the get picture function of the gui works basically, does not check for lost packet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
    [camera.cpp, main.cpp]
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2011-11-29 Add pull-up resistor that fixes camera issues
    [payload_644.sch]
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2011-12-14 Explain PCB image, fix introduction list.
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2011-12-15 Update schematic, layout with correct expansion header through hole sizes
    [payload_644.sch]
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2011-12-31 Rename gerbers to the extensions assigned by the new PCB release
    They were originally changed due to ECS' webmail thinking that .gbr
    files were actually viruses. Also, back -> bottom, front -> top, a
    logical change introduced by the new PCB, although maybe 'solder' and
    'component' (i.e. layer names) might make more sense.
    [payload_644.bottom.gbr, payload_644.bottommask.gbr, payload_644.bottompaste.gbr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]
2011-12-31 Add slightly updated PCB gerbers, from 4e22a8f
    This changed the expansion headers to their correct sizes
    [payload_644.bottom.gbr, payload_644.bottommask.gbr, payload_644.bottompaste.gbr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]
2012-01-09 Add a schematic for the surface mount component flavour of the payload
    [payload_smt.sch]
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

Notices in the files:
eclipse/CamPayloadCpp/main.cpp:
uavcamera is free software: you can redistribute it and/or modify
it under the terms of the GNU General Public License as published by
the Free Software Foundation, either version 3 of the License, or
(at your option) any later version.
